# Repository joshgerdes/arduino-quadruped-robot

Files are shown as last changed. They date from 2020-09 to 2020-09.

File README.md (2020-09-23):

# Arduino Quadruped Robot

An arduino power quadruped robot sprinter/walker based on the designs by Sebastian Coddington. This version uses a different codebase and has some modifications to the board and battery mounts.

<div style="display: flex;">
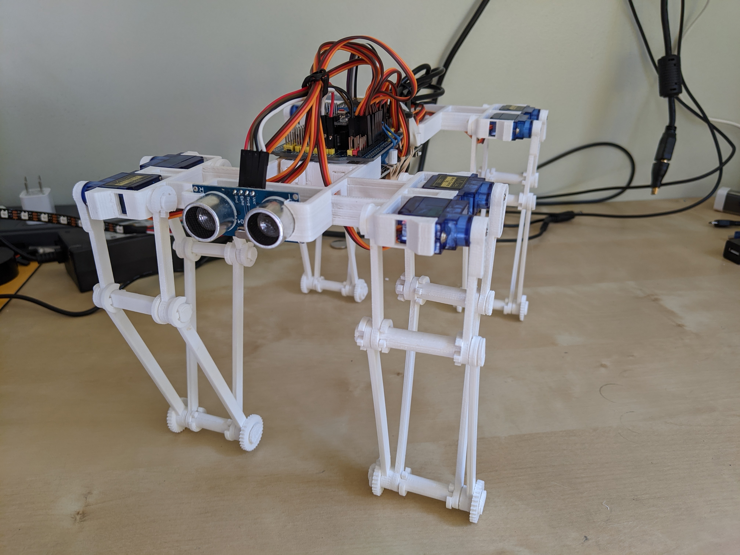
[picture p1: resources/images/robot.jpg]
Robot


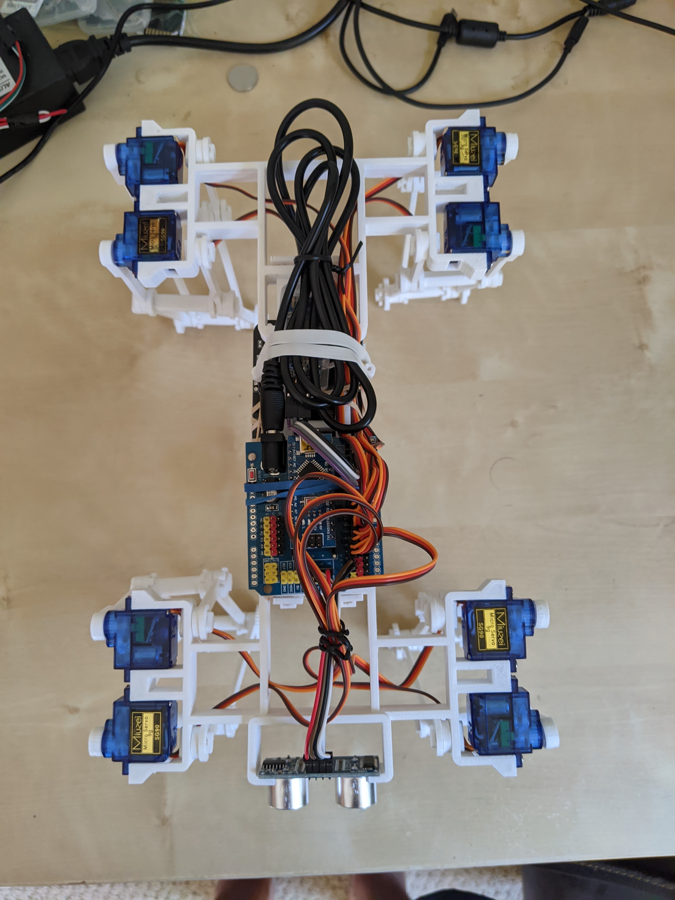
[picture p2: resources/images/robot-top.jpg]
Robot Top View


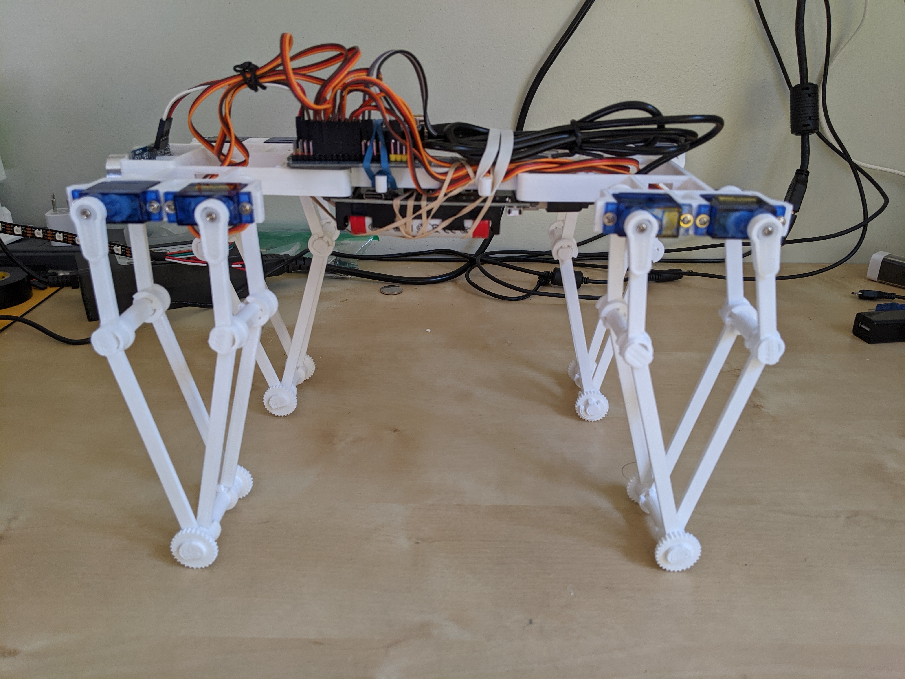
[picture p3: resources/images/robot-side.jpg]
Robot Side View

</div>

## Build Instructions

For the original robot, more detailed build and construction information can be found at: https://www.instructables.com/id/GorillaBot-the-3D-Printed-Arduino-Autonomous-Sprin/

## Wiring Diagram

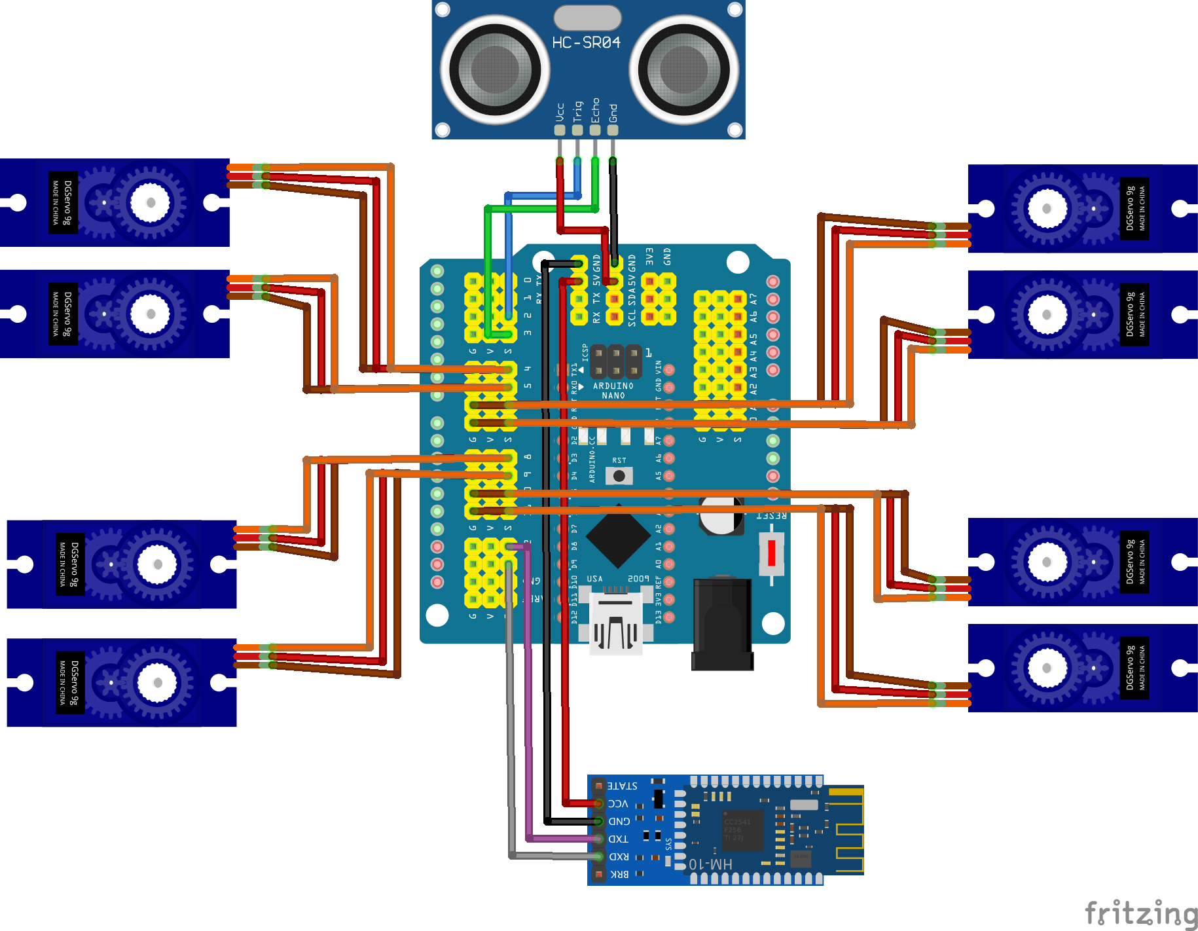
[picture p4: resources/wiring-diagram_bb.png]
Fritzing diagram sketch


## 3D Models

All new models were created in [Tinkercad](https://www.tinkercad.com/) and exported in STL format.

- [GROUP_BASE_BACK](resources/models/GROUP_BASE_BACK.stl)
- [GROUP_BASE_ELECTRONICS](resources/models/GROUP_BASE_ELECTRONICS.stl)
- [GROUP_BASE_FRONT](resources/models/GROUP_BASE_FRONT.stl)
- [GROUP_CIRCULAR_CLIPS](resources/models/GROUP_CIRCULAR_CLIPS.stl)
- [GROUP_CIRCULAR_PINS](resources/models/GROUP_CIRCULAR_PINS.stl)
- [GROUP_FEET_AND_SQUARE_CLIPS](resources/models/GROUP_FEET_AND_SQUARE_CLIPS.stl)
- [GROUP_LEGS_1](resources/models/GROUP_LEGS_1.stl)
- [GROUP_LEGS_2](resources/models/GROUP_LEGS_2.stl)
- [GROUP_LEGS_3](resources/models/GROUP_LEGS_3.stl)
- [GROUP_LEGS_4](resources/models/GROUP_LEGS_4.stl)

## Materials List

| Part | Qty | |
| --- | --- | --- |
| Arduino Nano V3.0 | 1 | https://amzn.to/2Ek0Rtx |
| Nano I/O Shield v3.0 (with 5v toggle switch) | 1 | https://ebay.to/2RIoyPs |
| Ultrasonic Module HC-SR04 Distance Sensor | 1 | https://amzn.to/3mFSaLz |
| HM-10 Bluetooth Module | 1 | https://amzn.to/2RIGpFQ |
| SG90 9G Micro Servos | 8 | https://amzn.to/3iU7odx |
| Breadboard Jumper Wires | 8 | https://amzn.to/2RKGrNF |
| 18650 Battery Shield | 1 | https://amzn.to/2FSBf7O |
| 18650 Batteries | 2 | https://amzn.to/32YADGJ |
| USB to DC 5.5 x 2.1mm 5V cable | 1 | https://amzn.to/2HuPrEN |

## Mobile App Configurations

I chose to drive the robot with the [ArduinoBlue](https://sites.google.com/stonybrook.edu/arduinoble/) mobile app and library. The joystick is preconfigured (for steering and throttle) but you will need to setup buttons initially to drive the remaining functionality. The following list of functions are available to setup as buttons within the app:

| ID  | Name | Description |
| --- | --- | --- |
| 1 | Autonomous | Toggle on/off autonomous mode |
| 2 | Stand | All legs in an up position |
| 3 | Lay | All legs in a down position |
| 4 | Sit | Back legs in down in a sitting position |
| 5 | Crouch | Front legs in down in a crouching position |
| 6 | Tilt | Tilting each leg in a clockwise rotation |
| 7 | Strut | Strut walk forward for a few paces |

## Libraries

- ArduinoBlue https://github.com/purwar2016/ArduinoBlue-library
- VarSpeedServo https://github.com/netlabtoolkit/VarSpeedServo

## Software & Other Resources

- Visual Studio Code - https://code.visualstudio.com/
- Arduino IDE - https://www.arduino.cc/en/Main/Software
- Ultimaker Cura - https://ultimaker.com/software/ultimaker-cura
- ArduinoBlue Mobile App - https://sites.google.com/stonybrook.edu/arduinoble/

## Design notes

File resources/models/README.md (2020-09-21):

GorillaBot the 3D Printed Arduino Autonomous Sprint Quadruped Robot by SebastianCoddington on Thingiverse: https://www.thingiverse.com/thing:4577379

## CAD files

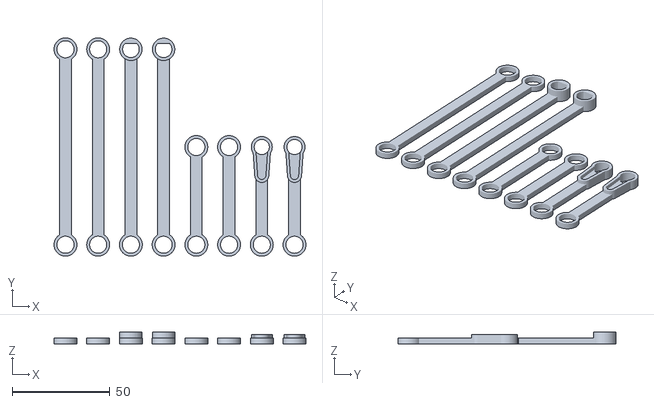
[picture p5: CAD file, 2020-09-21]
resources/models/GROUP_LEGS_3.stl
129.0 x 111.8 x 6.25

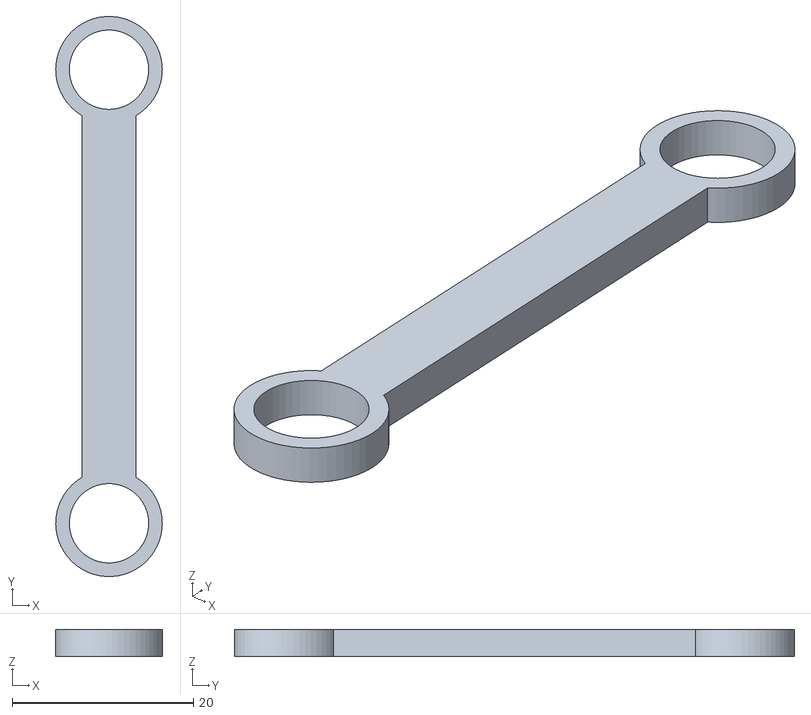
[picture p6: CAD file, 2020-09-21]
resources/models/INDIVIDUAL_THIGH.stl
11.7 x 61.7 x 3.00

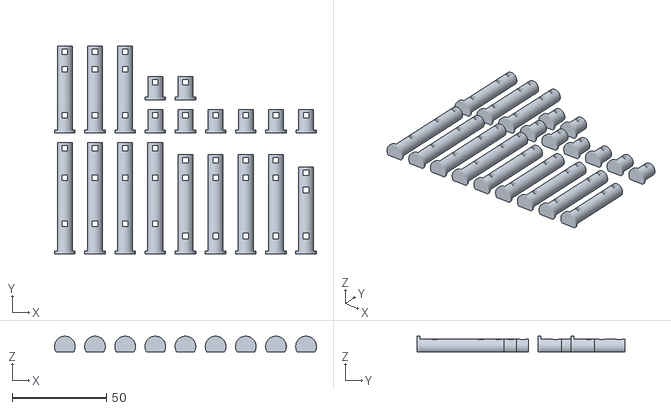
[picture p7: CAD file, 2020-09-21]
resources/models/GROUP_CIRCULAR_PINS.stl
139.0 x 110.2 x 8.33

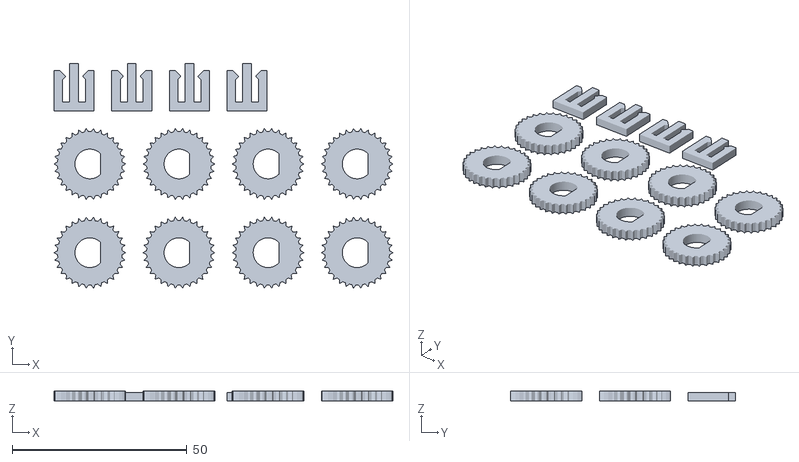
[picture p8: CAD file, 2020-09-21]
resources/models/GROUP_FEET_AND_SQUARE_CLIPS.stl
97.0 x 64.3 x 3.00

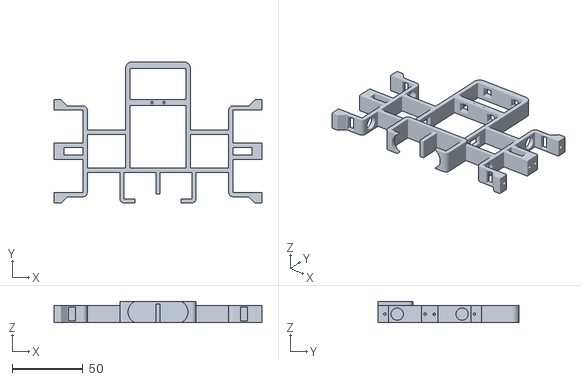
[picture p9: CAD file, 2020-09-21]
resources/models/GROUP_BASE_FRONT.stl
147.5 x 100.0 x 15.0

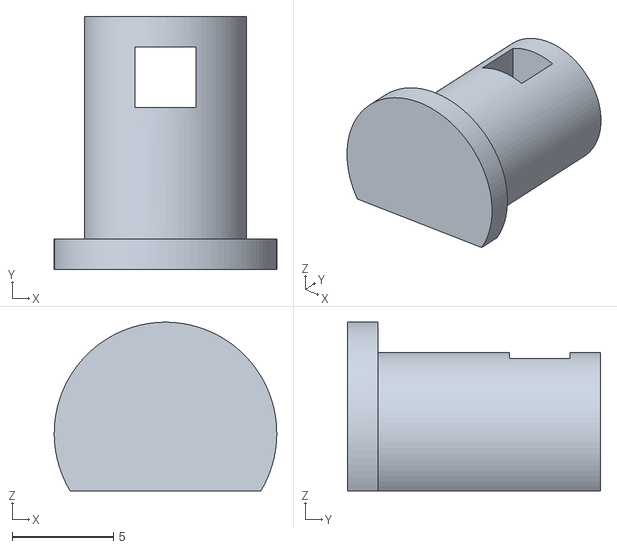
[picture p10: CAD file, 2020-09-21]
resources/models/INDIVIDUAL_CIRCULAR_PIN_L1.stl
11.0 x 12.5 x 8.33

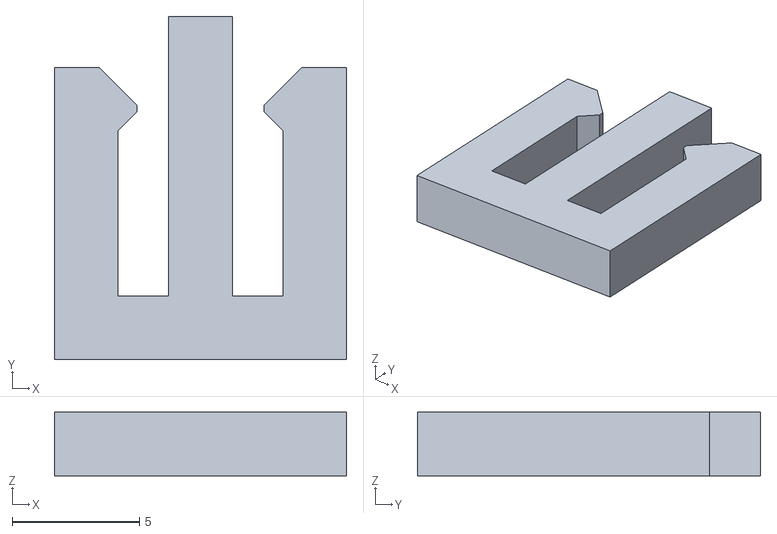
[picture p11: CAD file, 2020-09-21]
resources/models/INDIVIDUAL_SQUARE_CLIP.stl
11.5 x 13.5 x 2.50

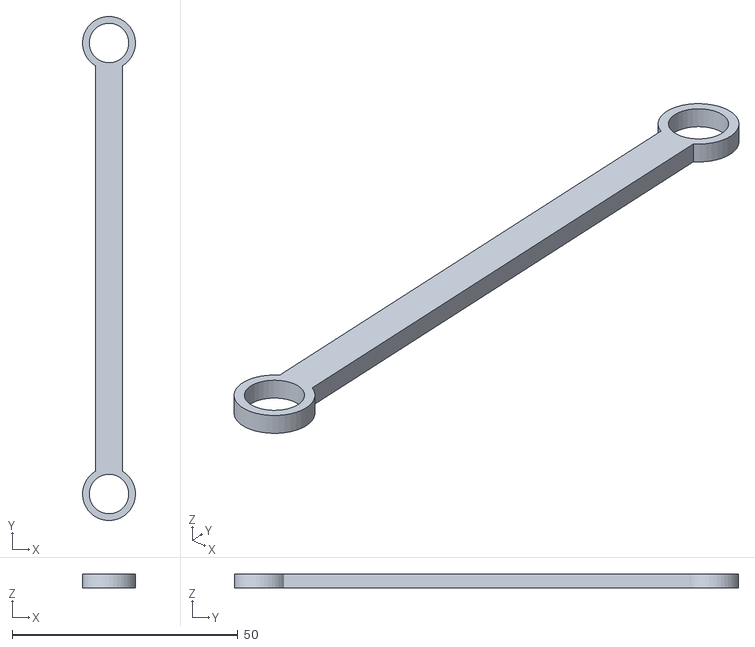
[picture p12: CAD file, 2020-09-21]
resources/models/INDIVIDUAL_CALF_INT.stl
11.7 x 111.8 x 3.00

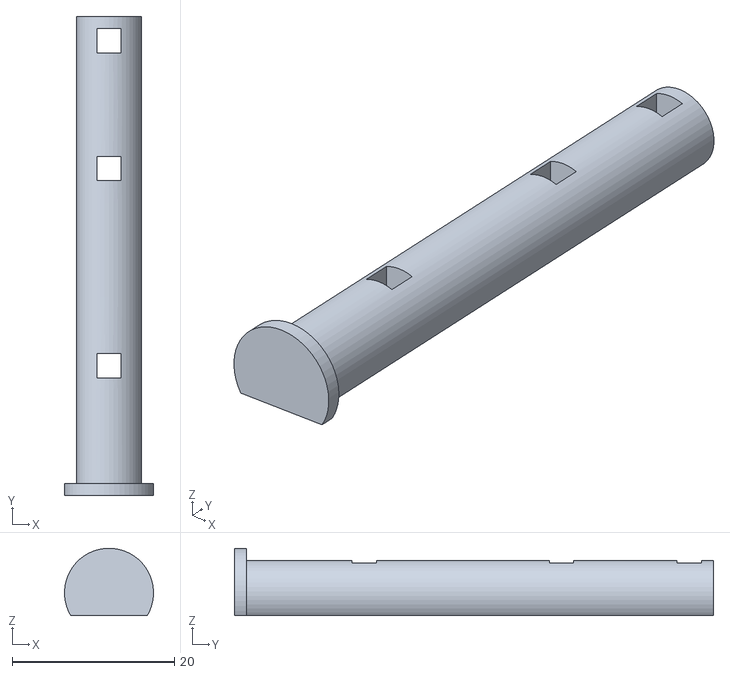
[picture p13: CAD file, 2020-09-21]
resources/models/INDIVIDUAL_CIRCULAR_PIN_L4.stl
11.0 x 59.1 x 8.33

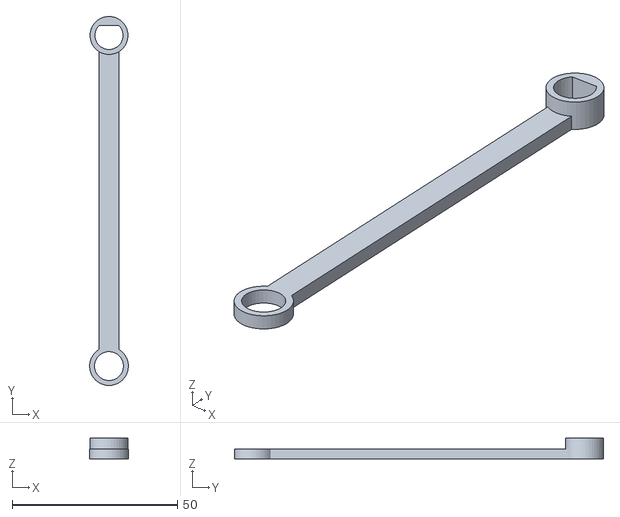
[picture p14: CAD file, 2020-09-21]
resources/models/INDIVIDUAL_CALF_EXT.stl
11.7 x 111.6 x 6.25

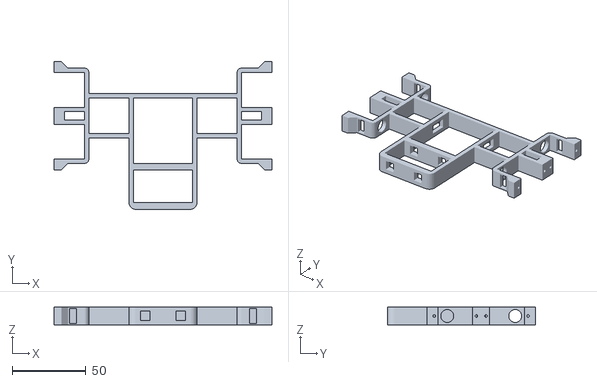
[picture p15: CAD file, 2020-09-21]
resources/models/INDIVIDUAL_BASE_BACK.stl
147.5 x 100.0 x 12.0

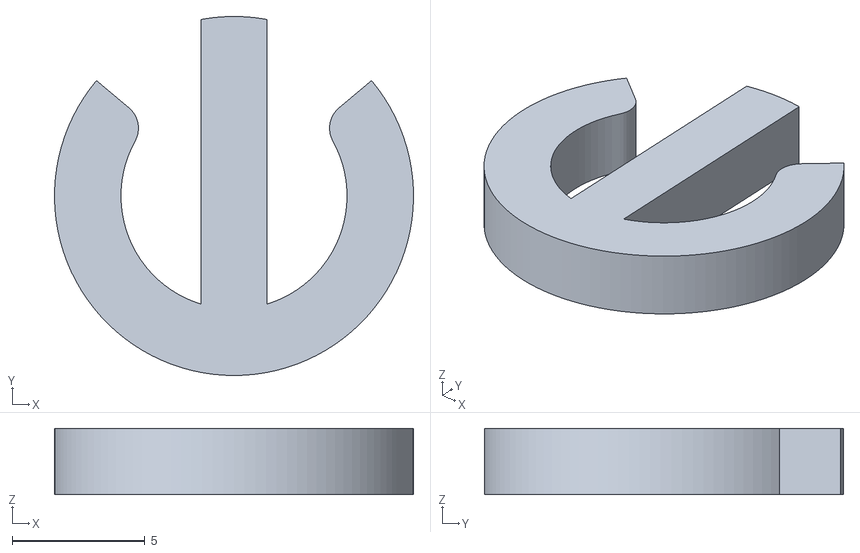
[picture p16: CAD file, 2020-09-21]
resources/models/INDIVIDUAL_CIRCULAR_CLIP.stl
13.5 x 13.5 x 2.50

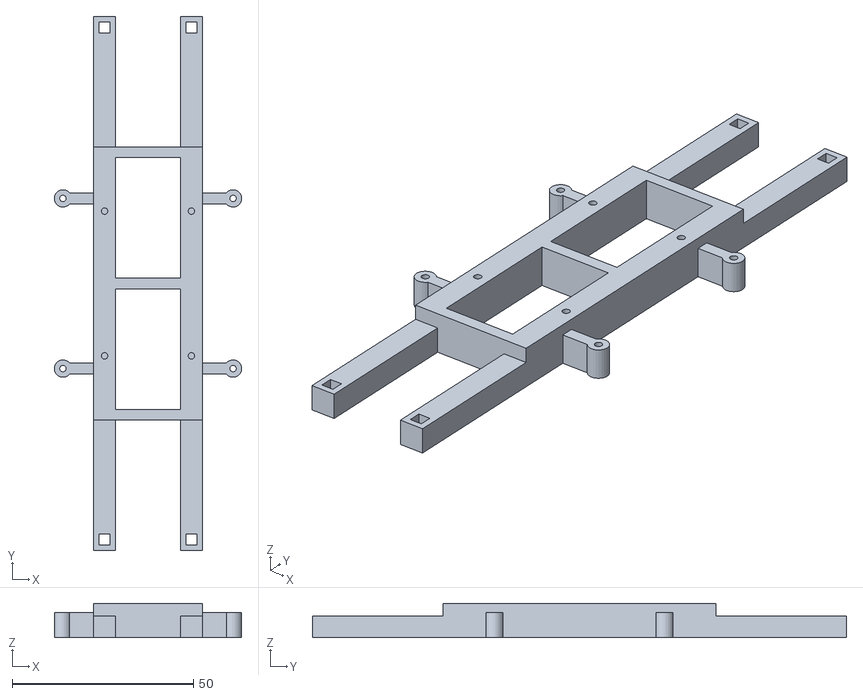
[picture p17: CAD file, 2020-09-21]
resources/models/INDIVIDUAL_BASE_ELECTRONICS.stl
51.8 x 147.5 x 9.50

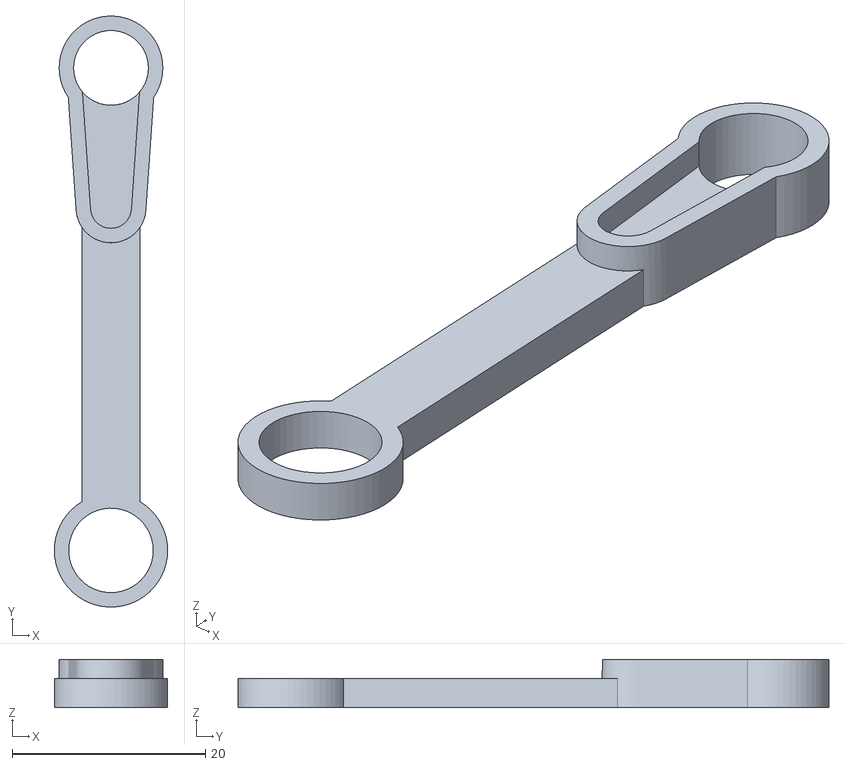
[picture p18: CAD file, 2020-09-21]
resources/models/INDIVIDUAL_THIGH_SERVO.stl
11.7 x 61.2 x 5.00

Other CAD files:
resources/models/INDIVIDUAL_CIRCULAR_PIN_L3.stl
resources/models/GROUP_BASE_BACK.stl
resources/models/GROUP_BASE_ELECTRONICS.stl
resources/models/GROUP_CIRCULAR_CLIPS.stl
resources/models/INDIVIDUAL_CIRCULAR_PIN_L2.stl
resources/models/INDIVIDUAL_FOOT.stl

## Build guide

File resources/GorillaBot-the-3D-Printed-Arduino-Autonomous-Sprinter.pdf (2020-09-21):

instructables

GorillaBot the 3D Printed Arduino Autonomous Sprint Quadruped Robot (http://www.instructables.com/id/GorillaBot-the-3D-Printed-Arduino-Autonomous-Sprin/)

by Sebastian Coddington (http://www.instructables.com/member/Sebastian+Coddington/)

Every year in Toulouse (France) there's the Toulouse Robot Race #TRR2021 (http://toulouse-robot-race.org/)

The race consists of a 10 meter autonomous sprint for biped and quadruped robots.

The current record I gather for quadrupeds is 42 seconds for a 10 meter sprint.

So with that in mind I had to come up with a plan of designing a robot that I thought could beat that in order to become the new reigning champion!!!

Seeking a bit of inspiration from a fellow Instructables member "jegatheesan.soundarapandian" and last year's winner of the Toulouse Robot Race "Oracid 1" who both seem to love designing and sharing tutorials on how to build quadrupeds. I got started on basically copying there design and making it a bit bigger!

The design is based on a ,ve bar linkage mechanism for each leg 2 servos power each leg for a total of 8 servos.

The rules state that apart from the start signal the whole race must be carried out by the robot autonomously so I had to come up with a light weight system to keep the robot on track in this case I used a QMC5883L Magnetometer (digital compass) so it could keep true to its orientation, a HC-SR04 Ultrasonic sensor in case the robot really messes up and starts hitting the wall at a 90 degree angle and I just used a step counter in the code to tell it how many steps it should do for 10 meters.

In case your interested in building this robot don't worry this monkey's got everything thought out!

100% Support free 3D print able Body:

Everything apart from the electronics and screws to attach the electronics are 3D printable, the same small cross head screws are the only ones used, all you'll need is a small cross head screwdriver to assemble the robot

Easy plug and play electronics :

no complex soldering required

Reasonable print time:

He may look big and imposing but he's only a 15 hour print (ok a long time for some :D)

Reasonable Build volume requirement s :

GorillaBot the 3D Printed Arduino Autonomous Sprint Quadruped Robot: Page 1

He can be printed on a relatively small printer requiring a build volume of only L:150mm x W:150mm x H: 25mm

Tot al robot cos t:

The robot alone costs around 75$ to build charger included

A 3D printed controller (https://www.instructables.com/id/3D-Printed-Arduino-Controller/) (optional) is required if you want the same set up as I have.

WARNING:

The 5V 3A power supply that I used isn't the best solution as for this robot to walk all 8 servos must run simultaneously and thus they draw quite a lot of current don't worry I haven't had the robot catch ,re or anything but expect the power transistor to heat up quite a bit I would not recommend using the robot for more than 2 minutes at a time letting it cool down between runs to avoid any unwanted damage to the Servo shield.

If any of you have a solution to this problem your input would be greatly appreciated!

Supplies:
SUPPLIES FOR THE ROBOT:

8x Tower Pro MG90S analog 180 deg servo (Aliexpress/Amazon)
1x Sunfounder Wireless Servo Control Board (Sunfounder Store/ RobotShop)
1x Arduino NANO (Aliexpress/Amazon)
1x NRF24L01 Transceiver Module(You don't need this if your not using the controller) (Aliexpress/Amazon)
1x Magnetometer (digital compass) QMC5883L GY-273 (Aliexpress/Amazon)
1x Ultrasonic sensor HC-SR04 (Aliexpress/Amazon)
2x 18650 3.7V Li-ion batteries (Aliexpress/Amazon)
1x 18650 dual Battery holder with on oI switch (Aliexpress/Amazon)
1x 18650 Li-ion Battery charger (Aliexpress/Amazon)
4x female to female dupont jumper cables 10 cm long (Aliexpress/Amazon)
4x female to female dupont jumper cables 20 cm long (Aliexpress/Amazon)
10x Screws 2mm x 8mm (same as the screws in a pack of servos) (Aliexpress/Amazon)

CONTROLLER:

To control this Robot manually you will need the 3D printed Arduino Controller (link here) (https://www.instructables.com/id/3D-Printed-Arduino-Controller/)

The Robot can also be purely autonomous so the controller is not mandatory.

PLAST ICS:

The parts can be printed in PLA or PETG or ABS.
GorillaBot the 3D Printed Arduino Autonomous Sprint Quadruped Robot: Page 2

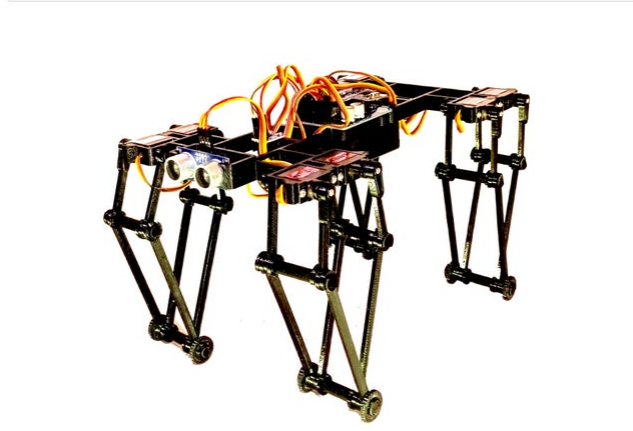
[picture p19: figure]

### Step 1: 3D Printing the Parts

!! Please note a 500g spool is more than enough to print 1 Robot !!

3D PRINT ER:

Minimum build platform required: L150mm x W150mm x H25mm

Any 3d printer will do. I personally printed the parts on the Creality Ender 3 which is a low cost 3D printer under 200$ The prints turned out perfectly.

https://youtu.be/nMdAFCHdepk

So now it's time for Printing...Yeay!

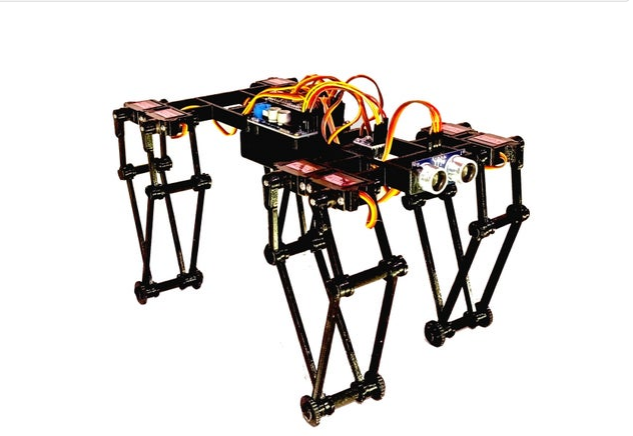
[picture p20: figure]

I Meticulously designed all of the parts to be 3D printed without any support materials required while printing.

All the parts are available to download on thingiverse (link here) (https://www.thingiverse.com/thing:4577379)

All the part s have been t es t print ed on the Crealit y Ender 3

Material: PETG
Layer Height: 0.3mm
In,ll: 15%
Nozzle diameter: 0.4mm

The part s lis t is as follows :

1x BASE ELECTRONICS
1x BASE BACK

GorillaBot the 3D Printed Arduino Autonomous Sprint Quadruped Robot: Page 3

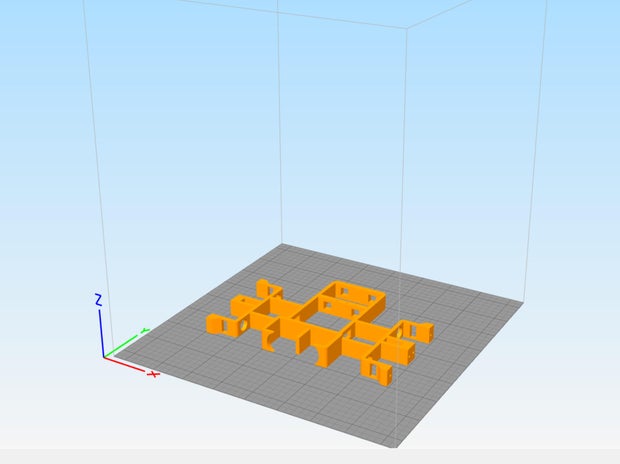
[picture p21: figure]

### Step 2: Assembling GorillaBot's Body

1x BASE FRONT
8x CIRCULAR PIN L1
4x CIRCULAR PIN L2
4x CIRCULAR PIN L3
4x CIRCULAR PIN L4
8x THIGH SERVO
8x THIGH
8x CALF EXT
8x CALF INT
8x FOOT
4x SQUARE CLIP
44x CIRCULAR CLIP

The ,les are available as individual parts and group parts.

For fast printing simply print every single GROUP.stl ,le once.

All the assembly instructions are depicted in the assembly video above:

1. Place a CIRCULAR PIN L1 in the hole of the BASE FRONT front left servo holder
2. Feed the cable of one of the MG90S servos through the slot in the BASE FRONT front left servo holder
3. Slot the MG90S servo in place
4. Secure the MG90S servo in place with 2 screws (do not over tighten as this could damage the BASE)
5. Repeat the same process for the BASE FRONT back left, front right and back right servo holders
6. Repeat the same process for the BASE BACK front left, back left, front right and back right servo holders
7. Secure the Battery holder to the BASE ELECTRONICS with 2 screws diagonally or 4 screws

GorillaBot the 3D Printed Arduino Autonomous Sprint Quadruped Robot: Page 4

### Step 3: Plugging in the Electronics

8. Secure the Wireless Servo Control Board to the BASE ELECTRONICS with 2 screws diagonally or 4 screws
9. Clip the Arduino nano and NRF24L01 transceiver to the Wireless Servo Control Board
10. Slide the BASE FRONT on to the BASE ELECTRONICS through the 2 square holes USB port facing back
11. Secure in place with 2 SQUARE CLIPS
12. Slide the BASE BACK on to the BASE ELECTRONICS through the 2 square holes USB port facing back
13. Secure in place with 2 SQUARE CLIPS
14. Secure the Magnetometer to the BASE FRONT with 2 screws
15. Clip the Ultrasonic sensor on to the BASE FRONT
16. Guide the servo cables towards the Wireless Servo Control Board as shown

https://youtu.be/j9515zVmRZM

All the connections are depicted in the Image above:

1. Plug the 4 20cm dupont cables in to the wireless servo control boards Ultrasonic pins
2. Plug the other end of the 4 cables in to the Ultrasonic sensor (Make sure they are the right way around)
3. Plug the 4 10cm dupont cables in to the wireless servo control boards Magnetometer pins
4. Plug the other end of the 4 cables in to the Magnetometer (Make sure they are the right way around)
5. Plug all the servos in to their dedicated pins in the wireless servo control board
6. Screw the battery VIN and GND wires to the wireless servo control board insure correct polarity

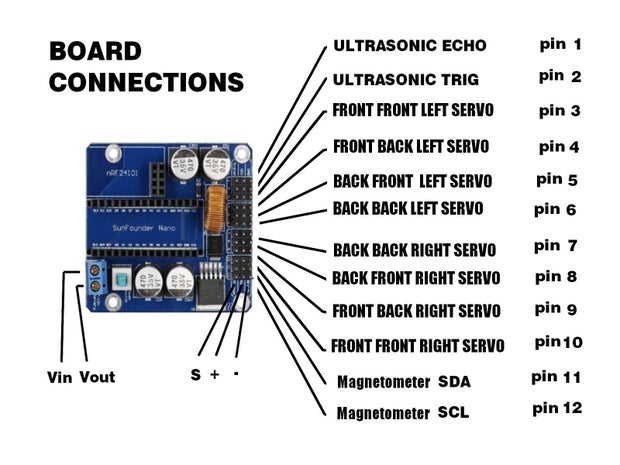
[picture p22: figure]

GorillaBot the 3D Printed Arduino Autonomous Sprint Quadruped Robot: Page 5

### Step 4: Assembling GorillaBot's Legs

### Step 5: Installing Arduino

All the assembly steps are depicted in the assembly video above:

1. Slide 1 FOOT over 1 CIRCULAR PIN L4
2. Slide the thicker end of 1 CALF EXT over the CIRCULAR PIN L4 with the sticking out side facing away from the foot
3. Slide 2 CALF INT over the CIRCULAR PIN L4
4. Slide the thicker end of 1 CALF EXT over the CIRCULAR PIN L4 with the sticking out side facing towards the foot
5. Slide 1 FOOT over the CIRCULAR PIN L4
6. Secure in place with 3 CIRCULAR CLIPS
7. Slide 1 CIRCULAR PIN L3 through 1 of the assembled CALF EXT
8. Slide 1 THIGH SERVO over the CIRCULAR PIN L3 with the sticking out side facing towards the CALF EXT
9. Slide 1 THIGH over the CIRCULAR PIN L3
10. Slide the CIRCULAR PIN L3 through the other assembled CALF EXT
11. Secure in place with 3 CIRCULAR CLIPS
12. Slide 1 THIGH SERVO over 1 CIRCULAR PIN L2 with the sticking out side facing towards the CIRCULAR PIN L2's head
13. Slide the CIRCULAR PIN L2 through both of the assembled CALF INTS
14. Slide 1 THIGH through the CIRCULAR PIN L2
15. Secure in place with 3 CIRCULAR CLIPS
16. Repeat all processes for the remaining 3 legs bare in mind that when the legs are assembled to the robot the pins heads face outwards and the CALF EXTS are in front of the CALF INTS so assembly will be identical front to back but symmetrical from left to right.

https://youtu.be/g1PQhhseAVc

GorillaBot uses C++ programming in order to function. In order to upload programs to GorillaBot we will be using Arduino IDE along with a few other libraries that need to be installed in the Arduino IDE.

Install Arduino IDE on to your computer: Arduino IDE (link here) (https://www.arduino.cc/en/Main/Software)

In order to install the libraries in to Arduino IDE you must do the following with all the libraries in the links below

1. Click on the links below (this will take you to the libraries GitHub page)
2. Click the green button that says Code
3. Click download ZIP (the download should start in your web browser)
4. Open the downloaded library folder
5. Unzip the downloaded library folder
GorillaBot the 3D Printed Arduino Autonomous Sprint Quadruped Robot: Page 6

### Step 6: Uploading the Code

### Step 7: Calibrating the Servos

6. Copy the unzipped library folder
7. Paste the unzipped library folder in to the Arduino library folder (C:\Documents\Arduino\libraries)

Libraries:

Varspeedservo library (link here) (https://github.com/netlabtoolkit/VarSpeedServo)
QMC5883L library (link here) (https://github.com/dthain/QMC5883L) RF24 Library (link here) (https://github.com/nRF24/RF24)

And there we have it you should be all ready to go In order to make sure you have correctly set up Arduino IDE follow the following steps

1. Download the desired Arduino Code below (GorillaBot Controller & Autonomous.ino)
2. Open it in Arduino IDE
3. Select Tools:
4. Select Board:
5. Select Arduino Nano
6. Select Tools:
7. Select Processor:
8. Select ATmega328p or ATmega328p (old bootloader) depending on which Arduino nano you purchased
9. Click the Verify button (Tick button) in the left upper corner of Arduino IDE

If all goes well you should get a message at the bottom that says Done compiling.

https://www.instructabl…

Download (https://content.instructables.com/ORIG/FX0/BYLH/KE48WV4Z/FX0BYLHKE48WV4Z.ino)

Now it's time to upload the code to GorillaBot's brain the Arduino Nano.

1. Plug the Arduino Nano in to your computer via USB cable
2. Click the upload button (Right arrow button)

If all goes well you should get a message at the bottom that says Done Uploading.

In order to assemble the legs correctly we must home the servos to their home position.

1. Insert 2 Li-ion Batteries in to the battery holder
2. Switch the robot on and wait 5 seconds for the servos to reach their home position GorillaBot the 3D Printed Arduino Autonomous Sprint Quadruped Robot: Page 7

### Step 8: Assembling Legs to Body

### Step 9: Ready to Race!!!

3. Switch the robot oI

Connecting the legs to the servos is pretty straightforward simply remember that the CALF EXT are to be placed in front of the CALF INT during assembly pin heads facing outwards.

1. Slide the THIGH of the CALF EXT side of one of the legs over the CIRCULAR PIN L1 on the front front left servo holder
2. Secure in place with 1 CIRCULAR CLIP
3. Slide the THIGH SERVO of the CALF EXT side of the same leg over the servo head on the front front left servo holder (Make sure the THIGH SERVO is at a 90 degree angle to the body)
4. Secure the THIGH SERVO in place at a 90 degree angle to the body with a single arm servo horn and small servo screw
5. Repeat the same process for the front back left servo holder with the remaining THIGH and THIGH SERVO of that leg
6. Repeat all previous processes for the remaining 3 legs

So that's it you should be all ready to go!!!

M anual mode:

Switch the robot and controller on and check that the robot walks properly by using the up down left and right directions of the Joystick.
Press the down button and the robot should perform a little dance

If everything works well the servos are well calibrated and you can now try out autonomous mode.

Autonomous mode

Autonomous Sprint mode uses the Magnetometer to keep the robot running in a constant direction for 2.5 meters. You can program the desired position and desired angle of correction using the controller

1. Switch the robot and controller on
2. Move the robot in all directions to calibrate the Magnetometer for 5 seconds
3. Place the robot on the ground in the desired position you would like him to go in
4. Press the up button to memorise that heading
5. Turn the robot 30-45 degrees to the left of desired heading
6. Press the left button to memorise that position
7. Turn the robot 30-45 degrees to the right of desired heading
8. Press the right button to memorise that position
GorillaBot the 3D Printed Arduino Autonomous Sprint Quadruped Robot: Page 8

In the section, Reasonable Build Volume, you have the dimensions in CM. This caught me off guard at first. But then I saw in the 3D printer section, you had the dimensions in mm. THat is MUCH more reasonable.

Nice build. Very interesting design.
Oh dear that doesn't sound so reasonable at all!! thanks for that I'll modify it
Can this robot turn in a circle or only walk staright?
Hey, Although the video only shows him turning for about 2 seconds in manual mode this robot can most definatly turn on the spot and quite quickly!
Nice bot | superb walk |
Thanks!

I like the way yours uses a Bluetooth app to control the robot and has a movable head!!! if you combine your electronics and coding with my leg design it would make a super cool robot!!!

It took me many prints to figure out what the biggest and fastest legs I could build while still only using MG90S servos

9. Place the robot back in to its desired heading
10. Press the joystick button to start the robot

The robot will run in a constant direction for 2.5 meters then stop sit and do a victory dance.

My robot managed to do the 2.5 meters in 7.5 seconds.

Which gives me a theoretical time of 10 meters in 30 seconds which hopefully will be enough to give me a good time at the Toulouse Robot Race

Wish me luck and for those of you who decide to build this robot I would love to hear your feedback and potential improvements that you think could be made!!!

GorillaBot the 3D Printed Arduino Autonomous Sprint Quadruped Robot: Page 9

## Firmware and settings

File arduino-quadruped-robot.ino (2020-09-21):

#include <SoftwareSerial.h>
#include "src/libraries/ArduinoBlue/src/ArduinoBlue.h"
#include "src/libraries/VarSpeedServo/VarSpeedServo.h"

#define BAUD_RATE 9600
#define BLUETOOTH_TX 13
#define BLUETOOTH_RX 12
#define PIN_TRIG 2
#define PIN_ECHO 3
#define STOP_MAX 75
#define STOP_MIN 25
#define DISTANCE_MIN 10

int throttle, steering, button, distance;
int prevThrottle = 49;
int prevSteering = 49;
bool autonomous = false;

SoftwareSerial bluetooth(BLUETOOTH_TX, BLUETOOTH_RX);
ArduinoBlue phone(bluetooth);

VarSpeedServo servoFrontLeftFront;
VarSpeedServo servoFrontLeftBack;
VarSpeedServo servoFrontRightFront;
VarSpeedServo servoFrontRightBack;
VarSpeedServo servoBackLeftFront;
VarSpeedServo servoBackLeftBack;
VarSpeedServo servoBackRightFront;
VarSpeedServo servoBackRightBack;

void setup()
{
  delay(3000); // power-up safety delay

  pinMode(PIN_TRIG, OUTPUT);
  pinMode(PIN_ECHO, INPUT);

  Serial.begin(BAUD_RATE);
  bluetooth.begin(BAUD_RATE);
  delay(100);

  stand();

  Serial.println("Setup Complete");
}

void loop()
{
  button = phone.getButton();
  throttle = phone.getThrottle();
  steering = phone.getSteering();
  distance = getDistance();

  logging();

  if (button == 1)
  {
    autonomous = !autonomous;
    stand();
  }

  if (autonomous)
  {
    autonomousMode();
  }
  else
  {
    standardMode();
  }
}

void autonomousMode()
{
  if (distance > DISTANCE_MIN)
  {
    forward();
  }
  else
  {
    tilt();
    delay(1000);
    sit();
    delay(1000);
    stand();

    for (int i = 0; i < 5; i++)
    {
      right();
    }
  }
}

void standardMode()
{
  if (button != -1)
  {
    switch (button)
    {
    case 2:
      stand();
      break;
    case 3:
      lay();
      break;
    case 4:
      sit();
      break;
    case 5:
      crouch();
      break;
    case 6:
      tilt();
      break;
    case 7:
      for (int i = 0; i < 5; i++)
      {
        strut();
      }
      break;
    }
  }
  else if (steering >= STOP_MAX)
  {
    right();
  }
  else if (steering <= STOP_MIN)
  {
    left();
  }
  else if (throttle >= STOP_MAX)
  {
    forward();
  }
  else if (throttle <= STOP_MIN)
  {
    backward();
  }
  else if (prevThrottle != throttle && prevSteering != steering)
  {
    stand();
  }

  prevThrottle = throttle;
  prevSteering = steering;
}

void logging()
{
  Serial.print("Button: ");
  Serial.print(button);
  Serial.print(", Throttle: ");
  Serial.print(throttle);
  Serial.print(", Steering: ");
  Serial.print(steering);
  Serial.print(", Distance: ");
  Serial.print(distance);
  Serial.print(", Autonomous: ");
  Serial.println(autonomous ? "True" : "False");
}

int getDistance()
{
  // Clears the PIN_TRIG condition
  digitalWrite(PIN_TRIG, LOW);
  delayMicroseconds(2);

  // Sets the PIN_TRIG HIGH (ACTIVE) for 10 microseconds
  digitalWrite(PIN_TRIG, HIGH);
  delayMicroseconds(10);
  digitalWrite(PIN_TRIG, LOW);

  // Reads the PIN_ECHO, returns the sound wave travel time in microseconds
  long duration = pulseIn(PIN_ECHO, HIGH);

  // Calculating the distance
  return duration * 0.034 / 2; // Speed of sound wave divided by 2 (go and back)
}

void servoAttach()
{
  servoFrontLeftFront.attach(4);
  servoFrontLeftBack.attach(5);
  servoFrontRightFront.attach(6);
  servoFrontRightBack.attach(7);
  servoBackLeftFront.attach(8);
  servoBackLeftBack.attach(9);
  servoBackRightFront.attach(10);
  servoBackRightBack.attach(11);
}

void servoDettach()
{
  servoFrontLeftFront.detach();
  servoFrontLeftBack.detach();
  servoFrontRightFront.detach();
  servoFrontRightBack.detach();
  servoBackLeftFront.detach();
  servoBackLeftBack.detach();
  servoBackRightFront.detach();
  servoBackRightBack.detach();
}

void move(int sFLF, int sFLB, int sFRF, int sFRB, int sBLF, int sBLB, int sBRF, int sBRB, int speed = 0, int delayed = 500, bool dettach = false)
{
  if (!servoFrontLeftFront.attached())
    servoAttach();

  servoFrontLeftFront.write(sFLF, speed);
  servoFrontLeftBack.write(sFLB, speed);
  servoFrontRightFront.write(sFRF, speed);
  servoFrontRightBack.write(sFRB, speed);
  servoBackLeftFront.write(sBLF, speed);
  servoBackLeftBack.write(sBLB, speed);
  servoBackRightFront.write(sBRF, speed);
  servoBackRightBack.write(sBRB, speed);

  delay(delayed);

  if (dettach)
    servoDettach();
}

void stand()
{
  move(180, 0, 0, 180, 180, 0, 0, 180, 0, 1000, true);
}

void lay()
{
  move(90, 90, 90, 90, 90, 90, 90, 90, 20, 2500, true);
}

void sit()
{
  move(180, 0, 0, 180, 45, 135, 135, 45, 150, true);
}

void crouch()
{
  move(45, 135, 135, 45, 180, 0, 0, 180, 150, true);
}

void tilt()
{
  int delayed = 400;
  int speed = 100;

  move(180, 0, 0, 180, 180, 0, 0, 180, 0, 1000);
  move(125, 55, 45, 135, 135, 45, 0, 180, speed, delayed);
  move(135, 45, 55, 125, 180, 0, 45, 135, speed, delayed);
  move(180, 0, 45, 135, 135, 45, 55, 125, speed, delayed);
  move(135, 45, 0, 180, 125, 55, 45, 135, speed, delayed);
  move(180, 0, 0, 180, 180, 0, 0, 180, 0, 1000, true);
}

void strut()
{
  int delayed = 150;

  move(180, 45, 0, 135, 180, 45, 0, 135, 0, delayed);
  move(90, 45, 0, 135, 180, 45, 90, 135, 0, delayed);
  move(135, 0, 0, 135, 180, 45, 45, 180, 0, delayed);
  move(180, 45, 0, 135, 180, 45, 0, 135, 0, delayed);
  move(180, 45, 90, 135, 90, 45, 0, 135, 0, delayed);
  move(180, 45, 45, 180, 135, 0, 0, 135, 0, delayed);
}

void forward()
{
  int delayed = 75;

  move(90, 135, 0, 135, 180, 45, 90, 45, 0, delayed);
  move(45, 0, 0, 135, 180, 45, 135, 180, 0, delayed);
  move(120, 0, 0, 135, 180, 45, 60, 180, 0, delayed);
  move(180, 45, 90, 45, 90, 135, 0, 135, 0, delayed);
  move(180, 45, 135, 180, 45, 0, 0, 135, 0, delayed);
  move(180, 45, 60, 180, 120, 0, 0, 135, 0, delayed);
}

void backward()
{
  int delayed = 75;

  move(45, 90, 45, 180, 135, 0, 135, 90, 0, delayed);
  move(180, 135, 45, 280, 235, 0, 0, 45, 0, delayed);
  move(180, 60, 45, 180, 135, 0, 0, 120, 0, delayed);
  move(135, 0, 135, 90, 45, 90, 45, 180, 0, delayed);
  move(135, 0, 0, 45, 180, 135, 45, 180, 0, delayed);
  move(135, 0, 0, 120, 180, 60, 45, 180, 0, delayed);
}

void left()
{
  int delayed = 75;

  move(0, 135, 90, 45, 45, 90, 135, 0, 0, delayed);
  move(0, 135, 135, 180, 180, 135, 135, 0, 0, delayed);
  move(0, 135, 60, 180, 180, 60, 135, 0, 0, delayed);
  move(90, 45, 0, 135, 135, 0, 45, 90, 0, delayed);
  move(135, 180, 0, 135, 135, 0, 180, 135, 0, delayed);
  move(60, 180, 0, 135, 135, 0, 180, 60, 0, delayed);
}

void right()
{
  int delayed = 75;

  move(90, 135, 180, 45, 45, 180, 135, 90, 0, delayed);
  move(45, 0, 180, 45, 45, 180, 0, 45, 0, delayed);
  move(120, 0, 180, 45, 45, 180, 0, 120, 0, delayed);
  move(180, 45, 90, 135, 135, 90, 45, 180, 0, delayed);
  move(180, 45, 45, 0, 0, 45, 45, 180, 0, delayed);
  move(180, 45, 120, 0, 0, 120, 45, 180, 0, delayed);
}

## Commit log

2020-09-21 Added 3D models
    [GROUP_BASE_BACK.stl, GROUP_BASE_ELECTRONICS.stl, GROUP_BASE_FRONT.stl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]
2020-09-23 Added documentation and wiring diagram
    [wiring-diagram_bb.fzz]
